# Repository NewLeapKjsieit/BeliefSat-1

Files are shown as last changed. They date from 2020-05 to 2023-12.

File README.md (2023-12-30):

# BeliefSat-1

BeliefSat-1 is a 2p-PocketQube standard student nano-satellite being developed by the undergraduate students of [**_K.J.Somaiya Institute of Engineering and Information Technology, Sion, Mumbai_** .](https://kjsieit.somaiya.edu/en) The satellite itself is a sub-part of team's proposal under [PS4-Orbital platform program](https://www.isro.gov.in/update/15-jun-2019/announcement-of-opportunity-ao-orbital-platform) of ISRO, wherein, team aims to demonstrate indegenously developed technologies for PocketQube standard nano-satellites. As a part of this demonstration, **BeliefSat** will be launched out of **SomaiyaPod** which is a Pocketqube standard deployer being indegenously developed at the institute. The unique construction technique, combination of COTS components for communication, on-board computer and power sub-systems , together constitute of **SomaiyaPQBus**, around which the satellite is being made, is also one of the technologies that the team wants to demonstrate and open-source to enable use by future missions.

## So what will BeliefSat do in space and what results it will give?

1. If it is successfully deployed out of the SomaiyaPod and completes startup procedure (it will be dead inside the Pod and will only get power after it is out of pod)and then sends a beacon; reliability of both deployer and the design of the satellite will be confirmed.
2. Every 1 minute, it will send a telemetry packet, which will have values from different COTS sensors. The team aims to project the activity of telemetry reception as a way of involving more students in to Software Defined Radio and RF in general.
3. It will have a functionality as of a amateur-radio digipeater. Which means if you hold a proper Amateur radio license then you can send a text message to the satellite and the satellite will repeat it (after delay of upto 10 seconds depending on other important processes running on-board). Making it a utility for Amateur radio community.
4. Not only it can digipeat a message it also has the functionality to repeat voice. For using this functionality you need a UHF transmitter and you can send a voice message to the satellite and the satellite will repeate it (after some delay depending on other important processes running on-board). It also will be a big utility for Amateur radio community.
5. If the satellite is able to operate for more than 3 months while responding to the commands and sending the health data at proper intervals, it will prove the reliablity of the unique design and set of COTS hardware used. Thus future mission could use flight proven hardwares for communication and power generation.

## What is it made of ?, What does it look like ?, What are its dimenssions and mass?

BeliefSat's structure is made by joining plates/PCBs(made out of FR4 material). This is a very novel approach in designing the structure of a satellite. Generally, satellites are made from Aluminium or its alloys, but using our novel approach we were able to design a very sturdy but cost effective sateliite. Although this technique is generally limited to nano-satellites. The PCBs that make the structure of our satellite have the solar panels and other components embedded in itself, so the complexity of assembly is minimized.

This is a concept render of our BeliefSat:

SATFOlded

The dimension of the BeliefSat is in accordance with the PocketQube Standards. This standard includes a base plate on which the satellite is mounted and then it slides out of
the satellite deployer via rails. As per the standards, our BeliefSat is 2P ie, Base plate is 58mm x 128mm x 1.6mm (WxLxH), whereas the satellite is 58mm x 128mm x 50mm (WxLxH).
The estimated mass of BeliefSat is around 450 grams. The dimensions of our deployer (SomaiyaPod) are 145mm x 200mm x 95mm (WxLxH).

## How is it powered?

The satellite is powered by AltaDevices Single Juntion cells ([which unfortunately are out of buisness as of date of writing](https://pv-magazine-usa.com/2019/12/31/shutdown-continues-at-hanergy-owned-alta-devices-high-efficiency-pv-pioneer/)). Each of these cell produce 0.25W power when illumniated at intensity of 1000W/m^2. There are 4 such cells on long sides and 2 on shorter sides. So when illuminated, satellite may produce 0.5W watt/1watt/>1W depending on the orientation. The power remaining after being used is then stored in 2 parallely connected [2600mah Samsung 18650 batteries](https://robokits.co.in/batteries-chargers/samsung-premium-li-ion-battery/3.7v-samsung-li-ion-batteries/samsung-icr-18650-26j-2600mah-li-ion-cell-original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). [SPV1040](https://www.st.com/en/power-management/spv1040.html) is used on every panel for maximum power point tracking and giving regulated voltage from the solar cells. The choice of SPV1040 was made based on flight history in [FossaSat-1](https://github.com/FOSSASystems/FOSSASAT-1). Now that AltaDevices cells won't be available in market, team will also be making one prototype with [SM141K06L by IXYS](https://www.digikey.com/product-detail/en/ixys/SM141K06L/SM141K06L-ND/9990462) and will be publishing test results for it too. 

## How does it communicate?

**_Transciever Specs_**
    **VHF**
-   **Name :** [DRA818V](http://www.dorji.com/products.php?Keyword=dra818v)
-   **Frequency Range :** 134~174 Mhz
-   **Channel Space :** 12.5/25 KHz
-   **TX Current :** 450/750 mA
-   **Temperature :** -20°C ~ +70°C
-   **Output Power :** +27/30 dbm
-   **Reciever Sensitivity :** -122 dbm (As per datasheet, observed sensititvity yet to be calculated)

    **UHF**
-   **Name :** [DRA818U](http://www.dorji.com/products.php?Keyword=dra818u)
-   **Frequency Range :** 400~470 Mhz
-   **Channel Space :** 25 KHz
-   **TX Current :** 450/750 mA
-   **Temperature :** -20°C ~ +70°C
-   **Output Power :** +27/30 dbm
-   **Reciever Sensitivity :** -122 dbm (As per datasheet, observed sensititvity yet to be calculated)
    _(UHF will only be used for voice repeater uplink)_
**_Antenna_**

Dipole made from measuring tape, which is in folded state during launch. Once in orbit, fishing cord which holds the antenna in folded position, is burnt by heating a resistor around which it is tied.

**_Link Budget_**

-   **Orbit Height :** 600 Km (proposed, may vary as per allocation by launch provider)
-   **Slant Range at 25 degree elevation :** 1213.4 Km (approximately)
-   **Free Space Path Loss at this distance for 145.825 MHz frequency :** 137.4 dbm
-   **Free Space Path Loss at this distance for 435.6 MHz frequency :** 146.9 dbm
-   **Received power neglecting mismatch,connector,atmospheric, pointing and polarization losses and receiving and transmitting antenna gains :** -118.2/-121.2 (op= 30/27dbm)
-   **Note :** A good directional antenna at receving groundstation (e.g. a 6 element yagi, plans for which will be released soon) can ensure the above mentioned losses are made up for and the signals can be received at even lower angles. However, to ensure best performance, circular polarized antennas copuled with a good LNA (e.g. [LNA4ALL](http://lna4all.blogspot.com/)) mounted over a Azimuth-Elevation antenna rotator (e.g. [Satnogs rotator](https://wiki.satnogs.org/SatNOGS_Rotator_v3)/[Sarcnet Rotator](https://www.sarcnet.org/rotator-mk2.html#RotatorMk2a)/[Yaesu G5500](https://www.yaesu.com/indexVS.cfm?cmd=DisplayProducts&ProdCatID=104&encProdID=79A89CEC477AA3B819EE02831F3FD5B8)/[WRAPS portable antenna rotator](https://ukamsat.files.wordpress.com/2013/12/wraps-mark-spencer-wa8sme-qst-jan-2014-copyright-arrl.pdf)) is recommended.

**_Data Rates in bps_**

-   **Telemetry Downlink :** 1200
-   **Digipeater Downlink :** 1200
-   **Command Uplink :** 1200
-   **Digipeater Uplink :** 1200

**_How the satellite complies with the requirment of turning off the transmitters when required ?_**
All the uplinks and downlinks occur on same frequency. Reciever is disabled while transmitting, to avoid interrupts to controller during the transmission, however, these transmissions last no more than 2 sec. This will ensure that one can relay a command during any pass. Also the transmitter is implemented to be active only when microcontroller is active, so if the main computer fails, the transmitter won't turn on. If the spacecraft computer is hung up for more than 8 sec, it resets along with the transciever. The automatic image capture mode is automatically turned off if battery voltage falls, thus adding extra layer of governance on the mode where long and continous transmission occurs. The satellite is designed to automatically turn off the microcontroller and thus the transciever in case of any thermal or short-circuit event. It is also protected against latchup situations caused by brown-outs or radiation flipping a bit, by the means of internal watchdog, which resets non-responsive or improperly finctioning controller after 8 sec. Whenever, required, satellites transmitters can be turned off until next command to turn those on by uplinking a command to do so. If the shut-down request comes when there is no pass over parent groundstation, the uplink packe format can be shared with a station which will have nearest pass.

## What are different packet types and packet formats ?

**_Telemetry Packet_**

**_APRS TELEMETRY FORMAT : The on-air packet telemetry format is as follows:_**

**T#sss,111,222,333,444,555,666,777,888,999,AAA,xxxxxxxx**
where,
-    sss : LSB of total number of system resets
-    111 : MSB of total number of system resets
-    222 : LSB of total number of resets induced by watch dog
-    333 : MSB of total number of resets induced by watch dog
-    444 : Temperature sensor 1 reading
-    555 : Temperature sensor 2 reading
-    666 : Gyro-sensor 1 reading
-    777 : Gyro-sensor 1 reading
-    888 : Gyro-sensor 1 reading
-    999 : Current reading
-    AAA : Voltage reading
-    xxxxxxxx : If the last two bits are 10 then digipeater is on and if they are 01 then voice repeater is on.

**References for converting Sensor data into readable format**

1. Temperature Sensor (DS18B20) :- [Datasheet](https://pdf1.alldatasheet.com/datasheet-pdf/view/58557/DALLAS/DS18B20.html)

2. Gyro Sensor (MPU-6050) :- [Datasheet](https://invensense.tdk.com/wp-content/uploads/2015/02/MPU-6000-Datasheet1.pdf)

3. Current/Power Sensor (INA219) :- [Datasheet](https://www.ti.com/lit/ds/symlink/ina219.pdf?ts=1593455980944&ref_url=https%253A%252F%252Fwww.google.com%252F)

**Reference for transreceivers**

1. DRA818V :- [Datasheet](http://www.dorji.com/docs/data/DRA818V.pdf)

2. DRA818U :- [Datasheet](http://www.dorji.com/docs/data/DRA818U.pdf)

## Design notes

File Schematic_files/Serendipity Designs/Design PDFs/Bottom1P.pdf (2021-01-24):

23-10-2020 11:05 PM C:\Users\Manas R. Sable\Desktop\PROTOTYPE\Final PCBs\BOTTOM_1P.sch (Sheet: 1/1) | 10K

A

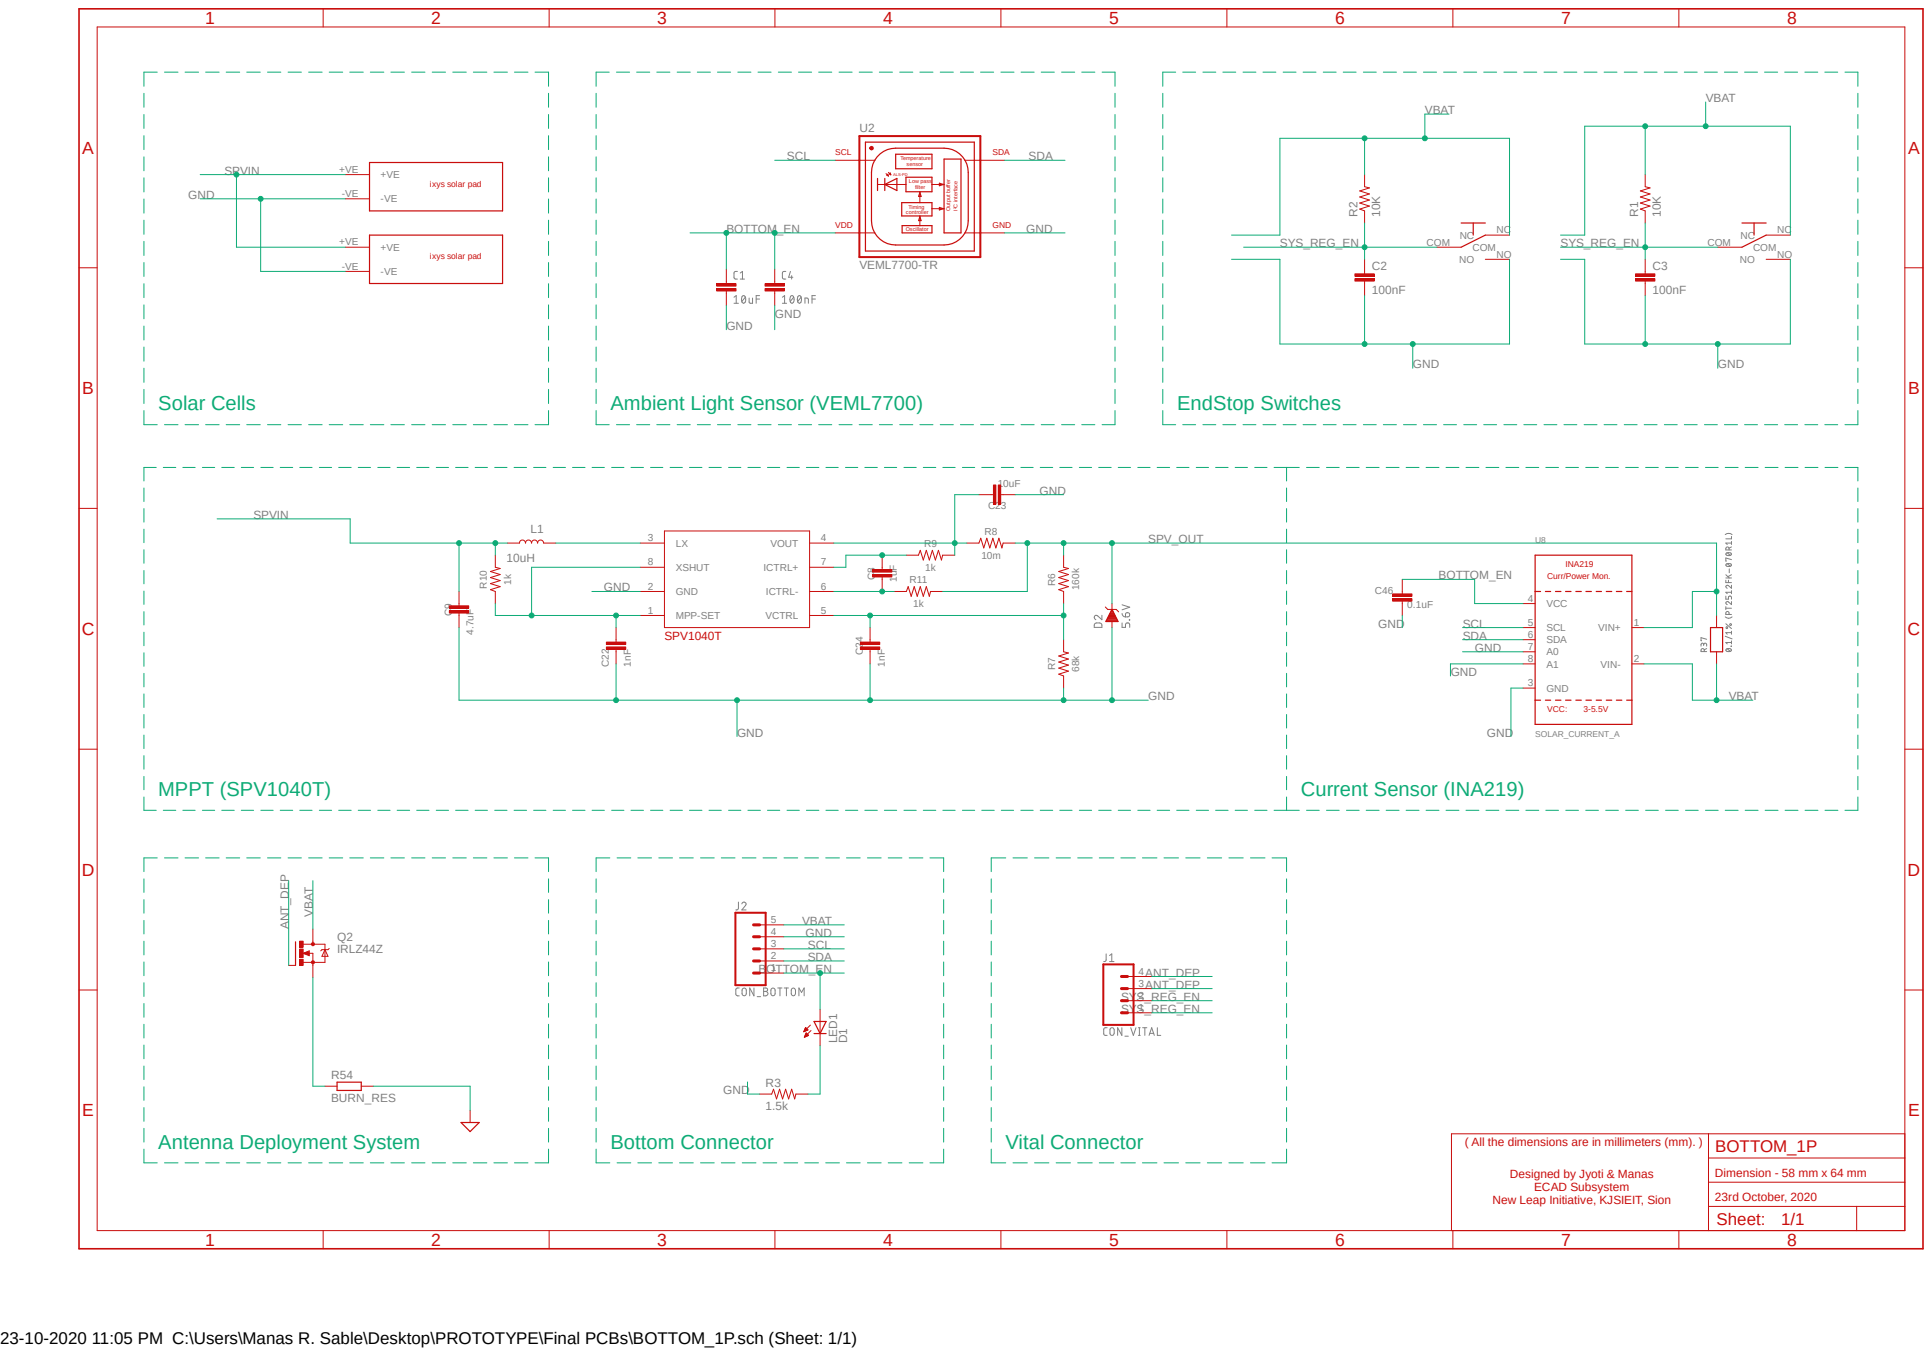
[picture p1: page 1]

( All the dimensions are in millimeters (mm). )

Designed by Jyoti & Manas
ECAD Subsystem

New Leap Initiative, KJSIEIT, Sion

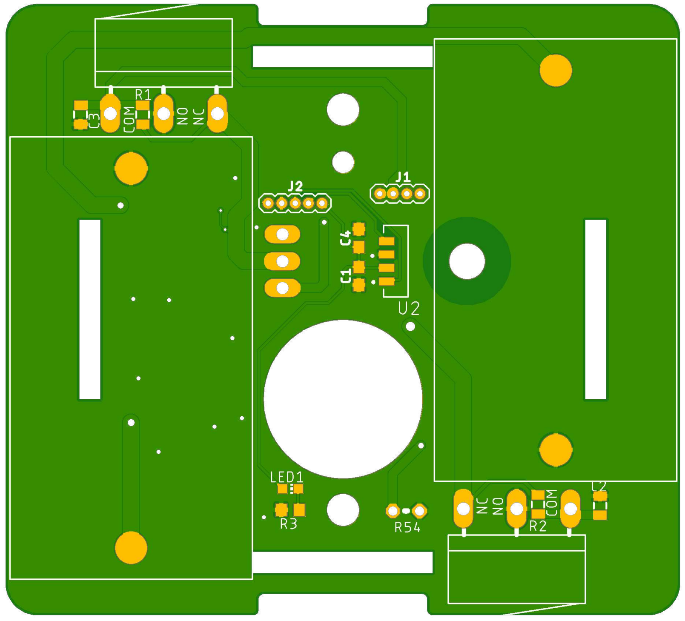
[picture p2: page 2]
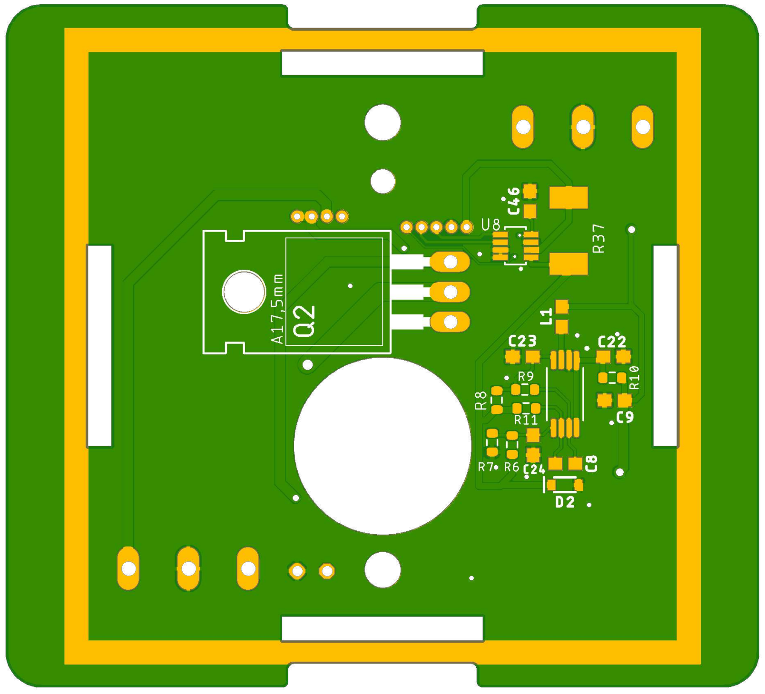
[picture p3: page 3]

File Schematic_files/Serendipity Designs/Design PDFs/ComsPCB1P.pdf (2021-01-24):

A

A

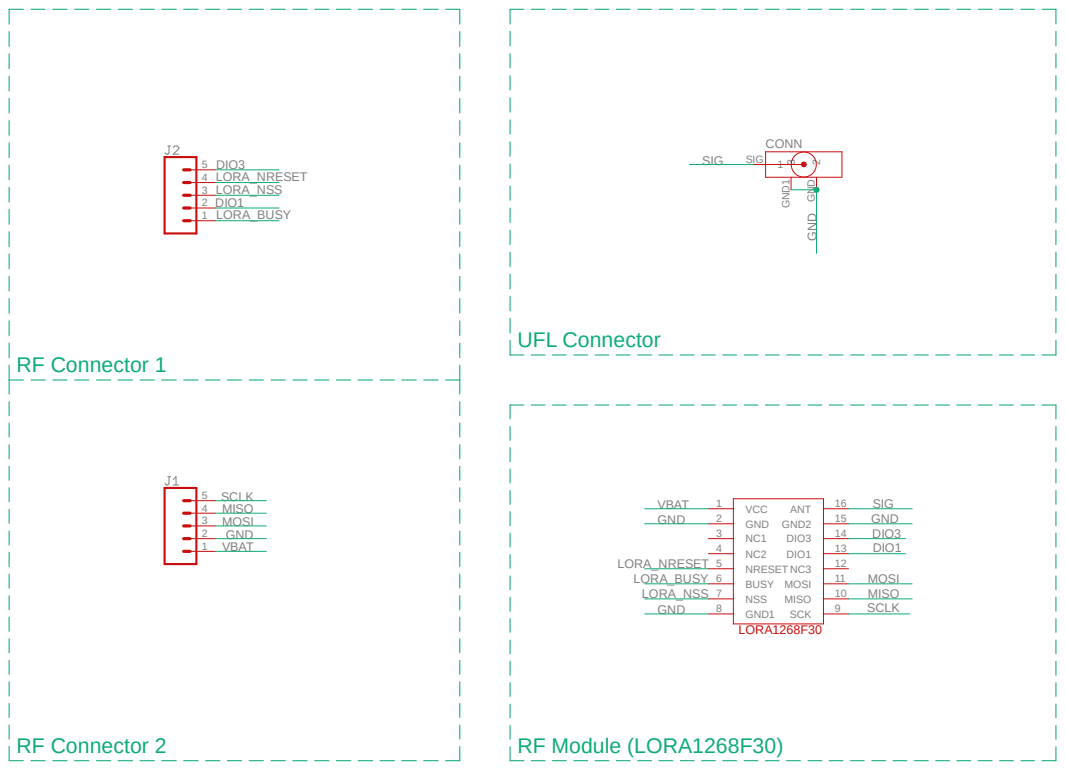
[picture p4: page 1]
1 SIG; 3 GND¹; 2 GND; CONN; VCC 1; GND 2; NRESET 5; BUSY 6; NSS 7; GND1 8; SCK; 9 MISO; 10 MOSI; 12 DIO1; 13 DIO3; 14 GND2; 15 ANT; 16 VBAT; VBAT; GND; MOSI; MISO; SCLK; LORA_BUSY; LORA_NSS; LORA_NRESET; SIG; DIO3; DIO1; LORA1268F30; ComsPCB (1); RF Module (LORA1268F30); UFL Connector; RF Connector 1; RF Connector 2

( All the dimensions are in millimeters (mm). )

Designed by Jyoti & Manas
ECAD Subsystem

Dimension - 42 mm x 44 mm
24th October, 2020
Sheet:

New Leap Initiative, KJSIEIT, Sion

24-10-2020 07:42 PM C:\Users\Manas R. Sable\Desktop\PROTOTYPE\Final PCBs\ComsPCB (1).sch (Sheet: 1/1)

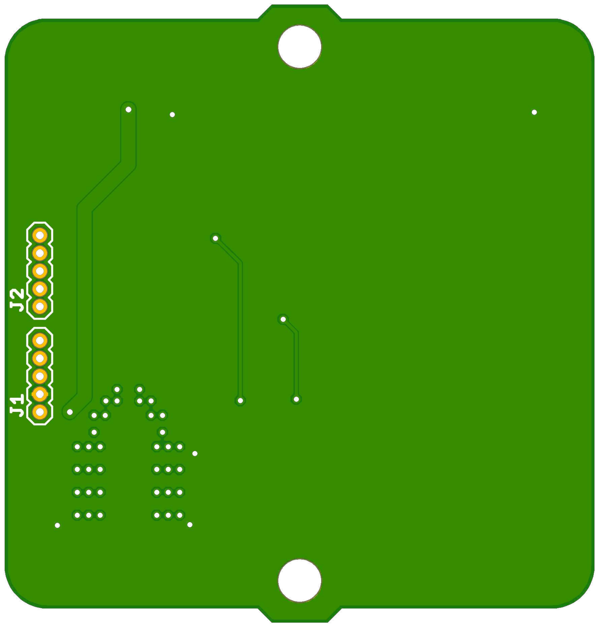
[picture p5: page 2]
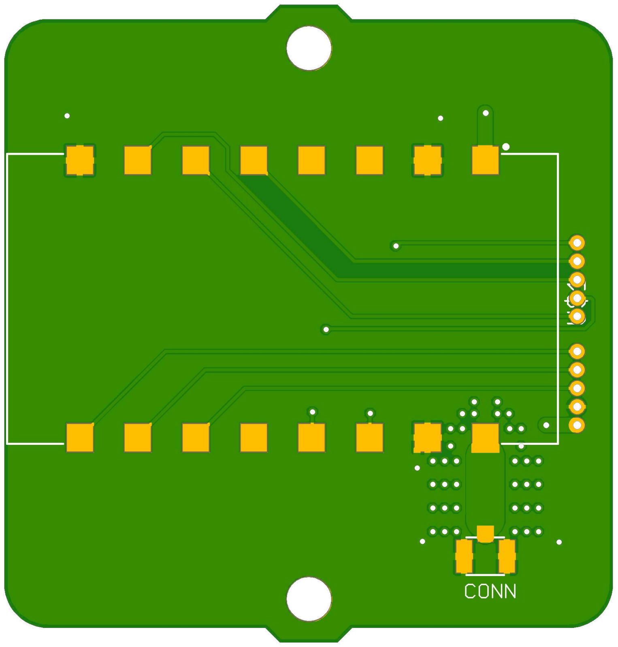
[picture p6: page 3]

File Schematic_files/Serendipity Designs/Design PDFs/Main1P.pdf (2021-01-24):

A

A

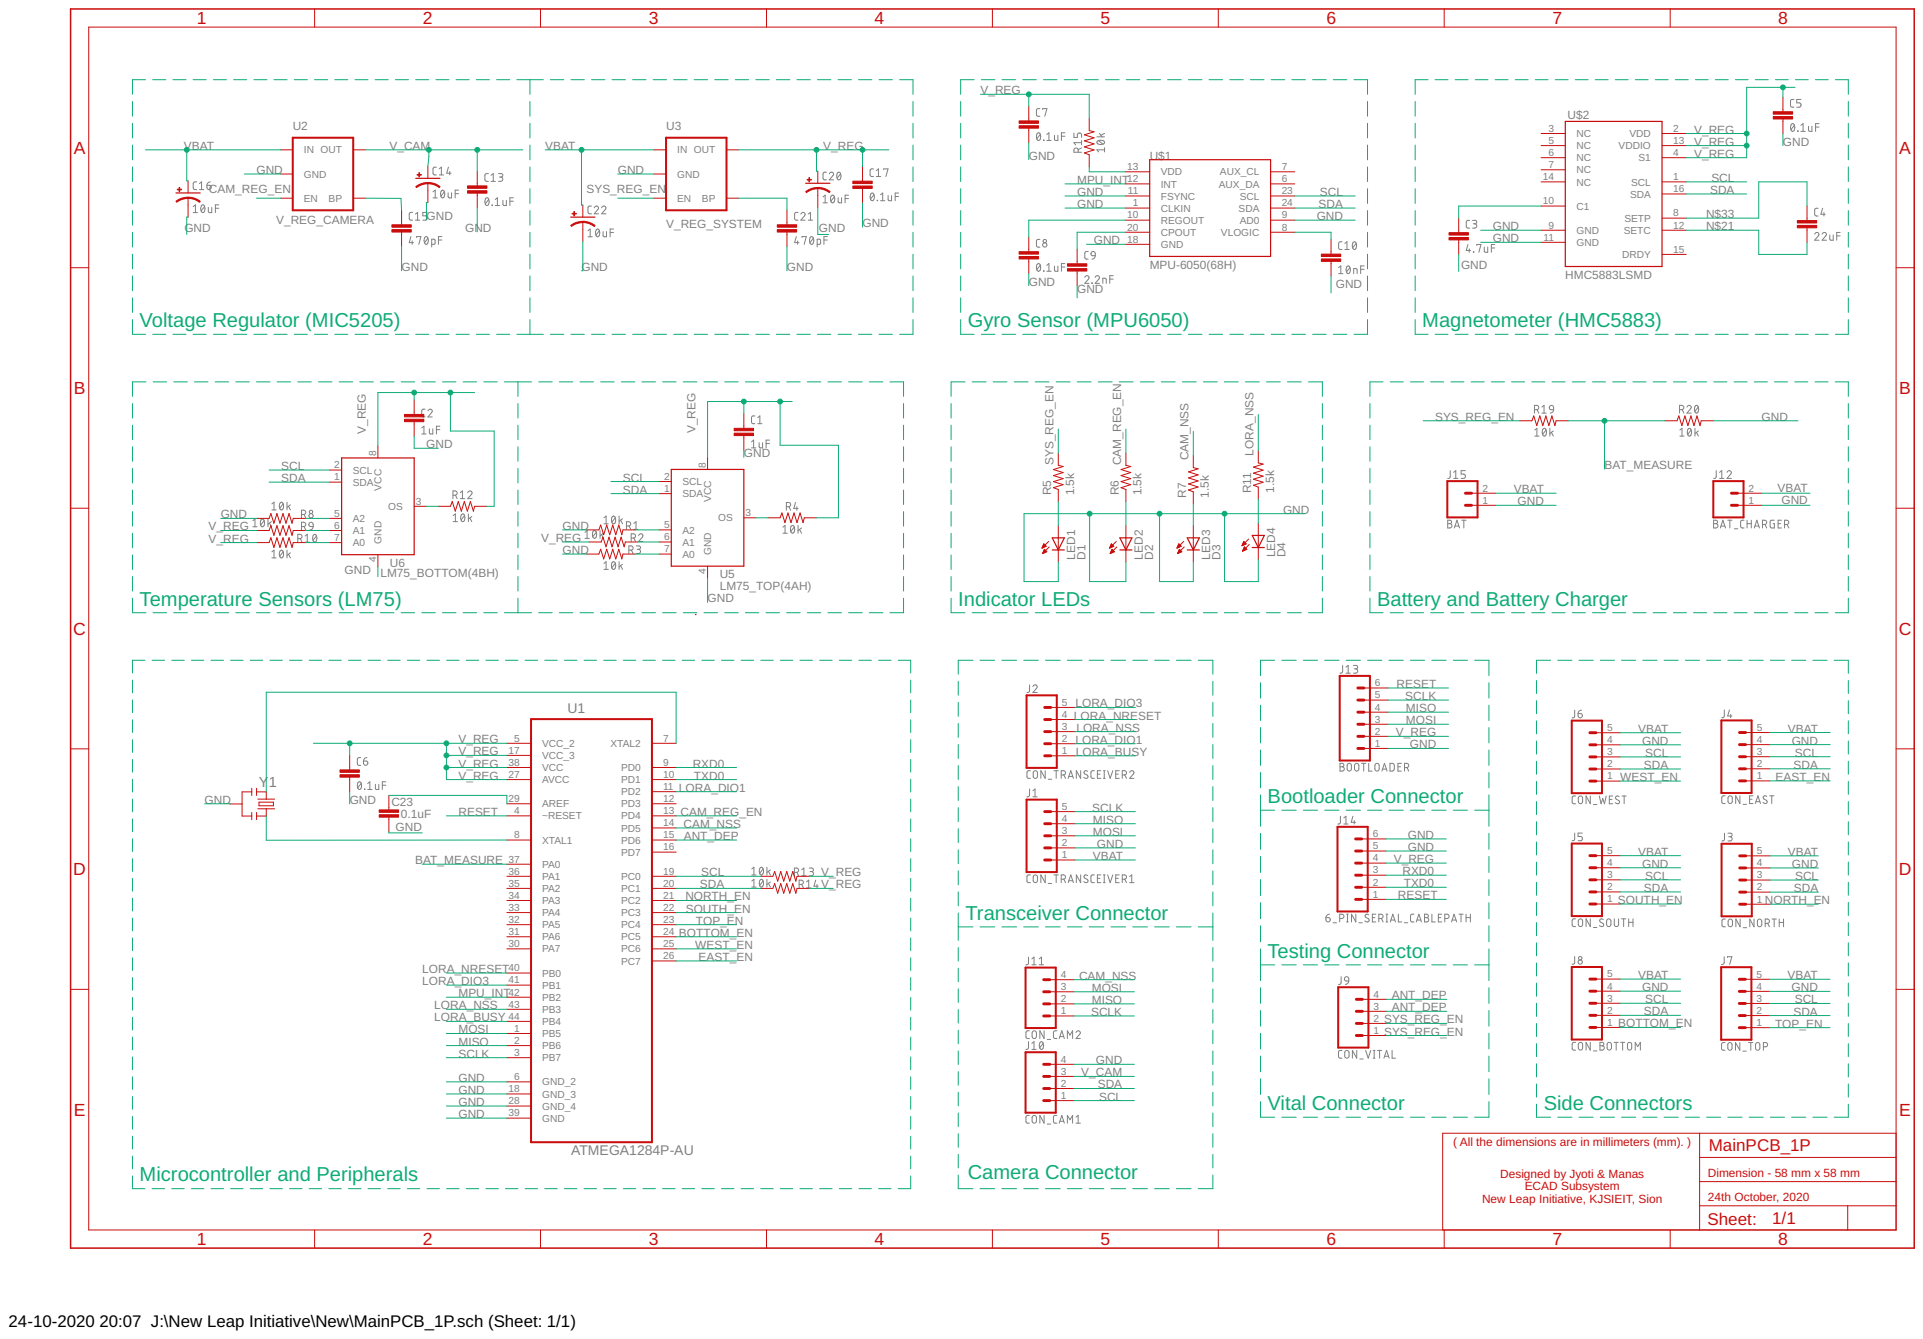
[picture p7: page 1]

( All the dimensions are in millimeters (mm). )

Designed by Jyoti & Manas ECAD Subsystem

24-10-2020 20:07 J:\New Leap Initiative\New\MainPCB_1P.sch (Sheet: 1/1)

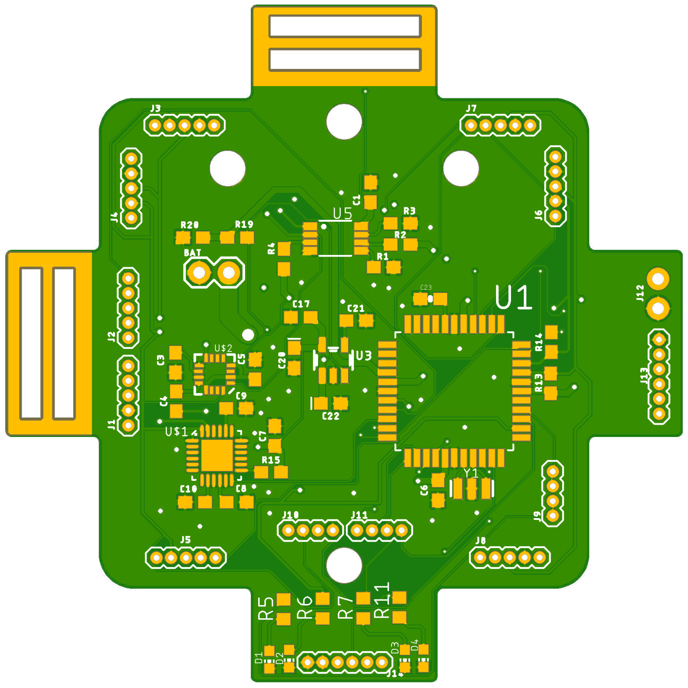
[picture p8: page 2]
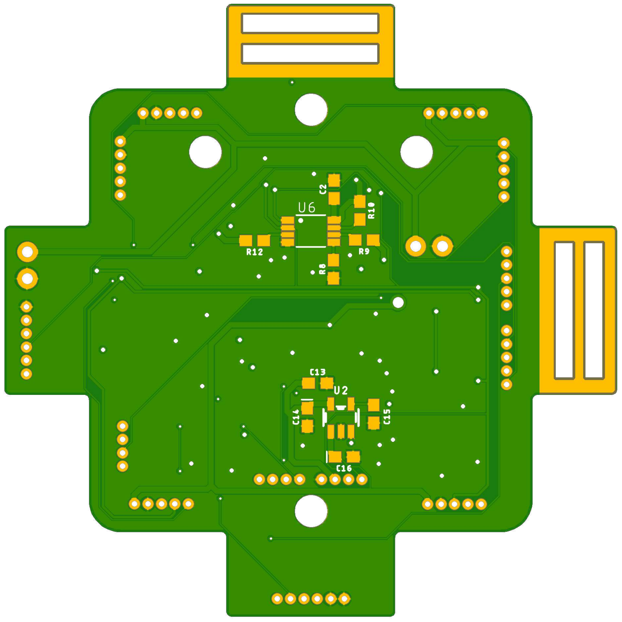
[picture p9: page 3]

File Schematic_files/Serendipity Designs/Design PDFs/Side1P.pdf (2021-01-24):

A

A

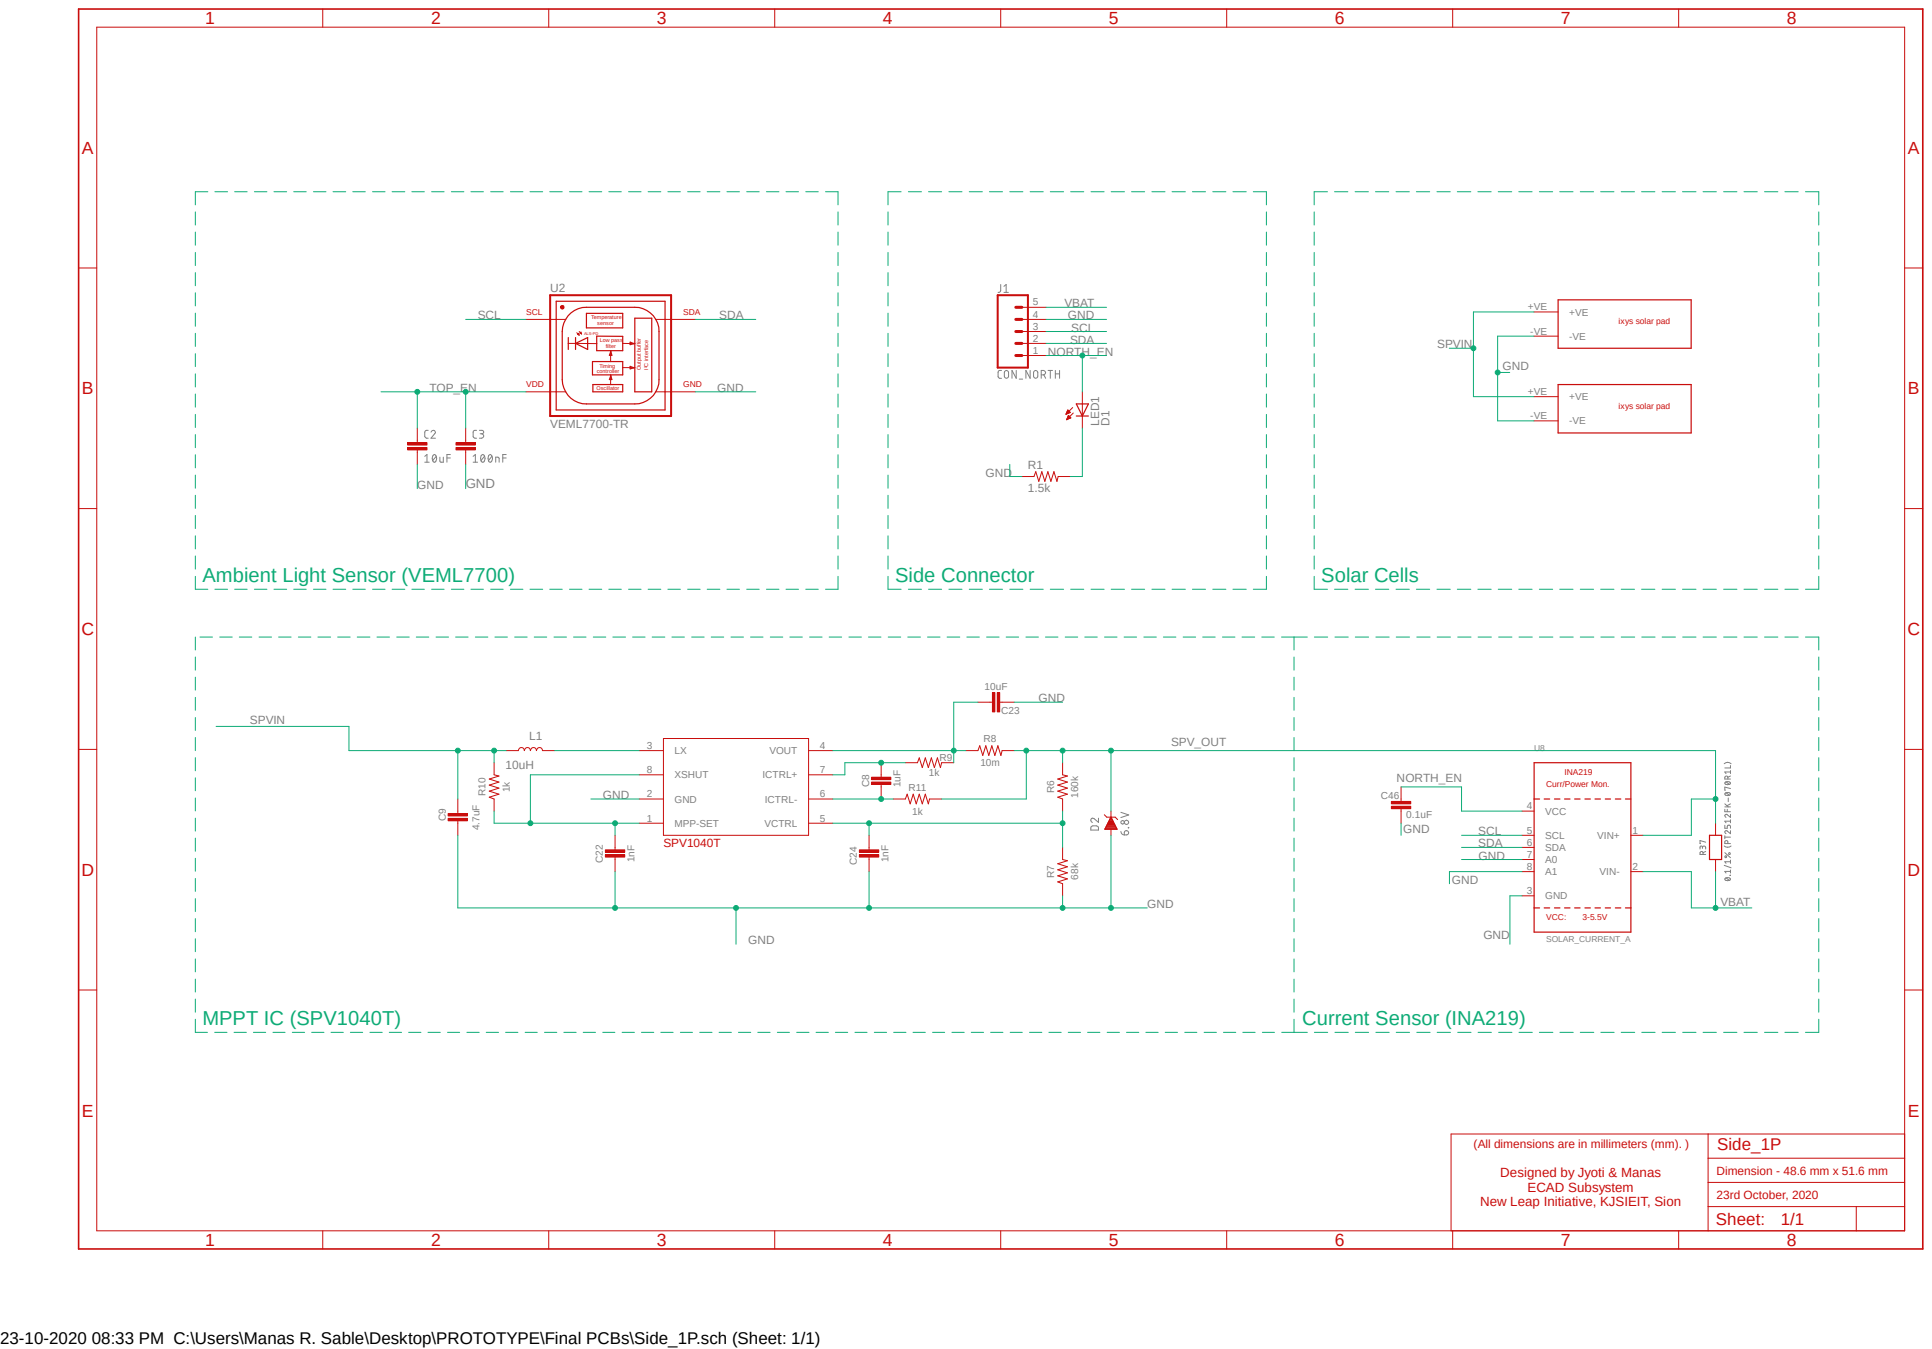
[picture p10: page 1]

(All dimensions are in millimeters (mm). )
Designed by Jyoti & Manas
ECAD Subsystem

New Leap Initiative, KJSIEIT, Sion

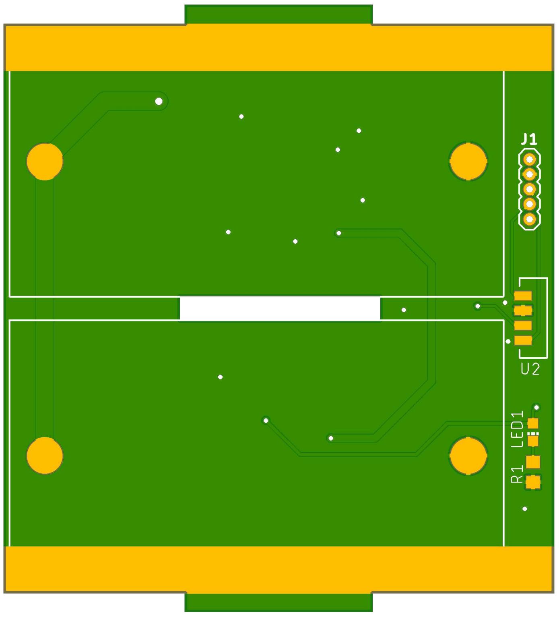
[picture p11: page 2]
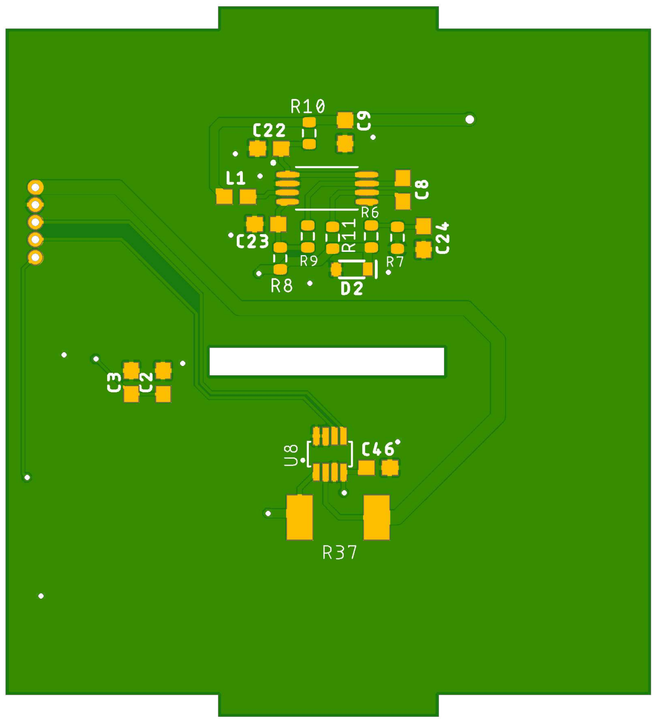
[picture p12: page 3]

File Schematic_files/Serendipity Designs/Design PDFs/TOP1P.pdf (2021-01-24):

A

A

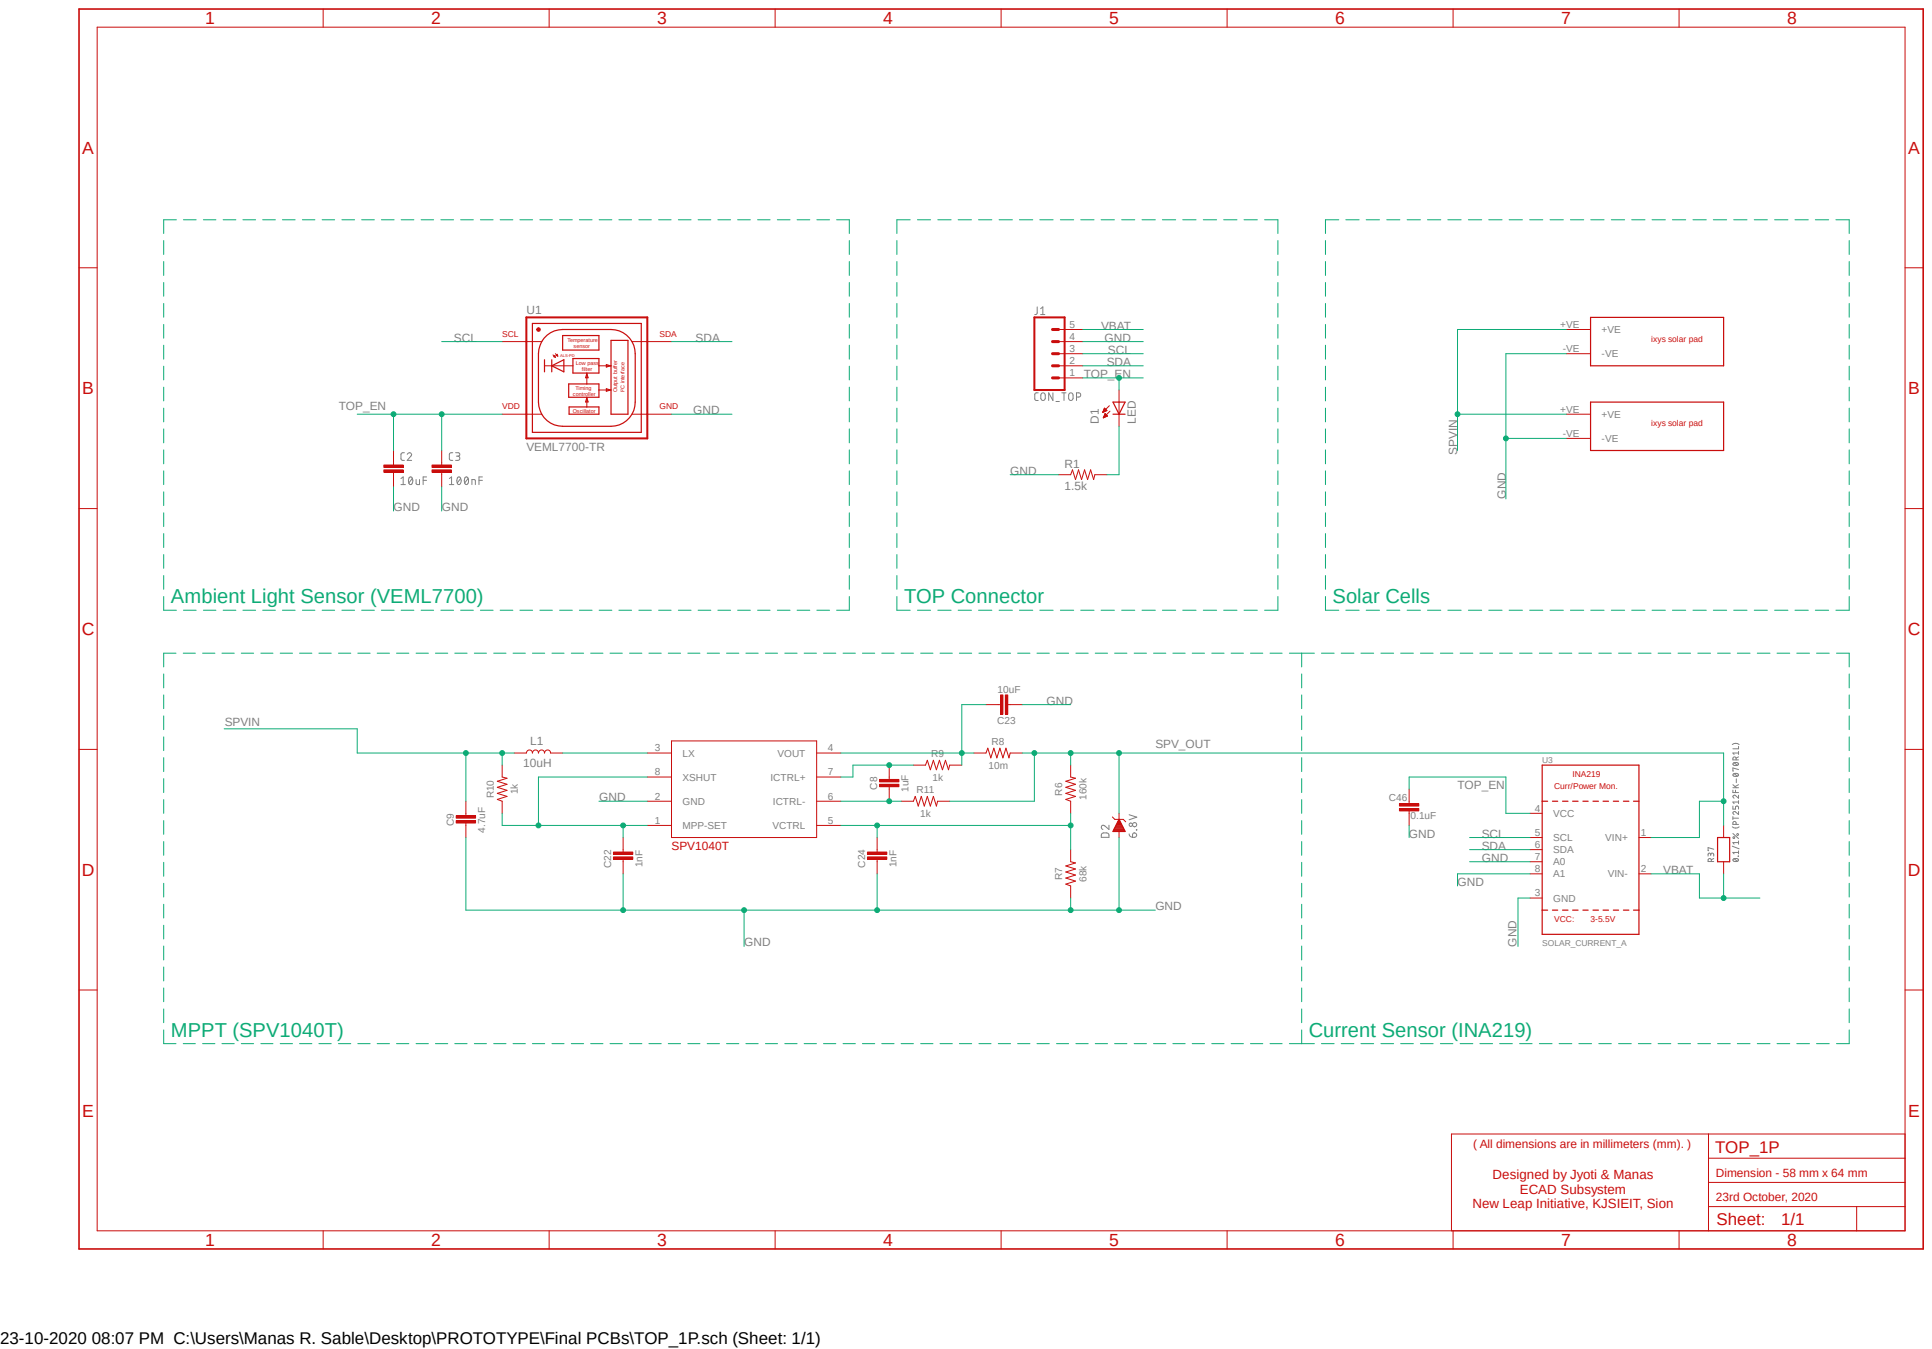
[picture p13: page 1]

( All dimensions are in millimeters (mm). )

Designed by Jyoti & Manas
ECAD Subsystem

New Leap Initiative, KJSIEIT, Sion

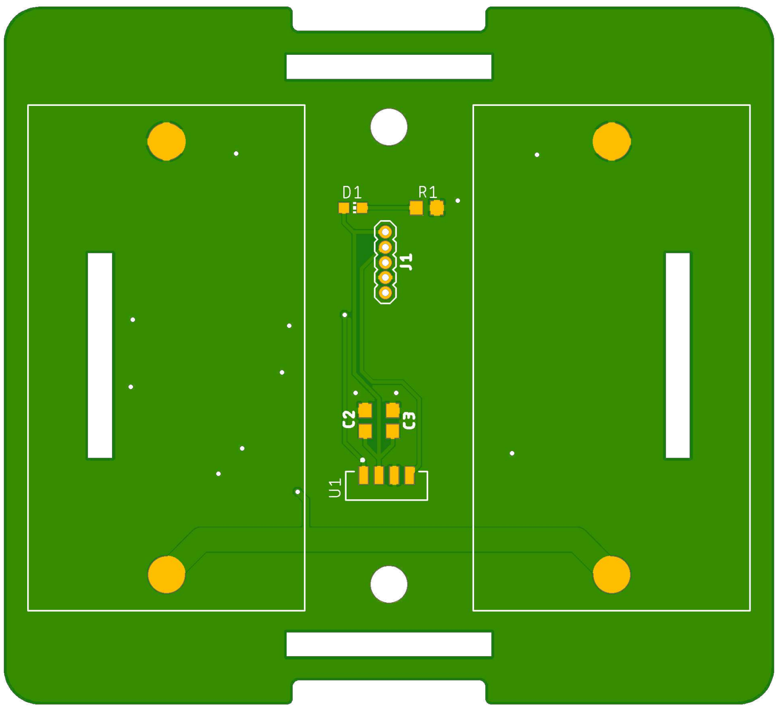
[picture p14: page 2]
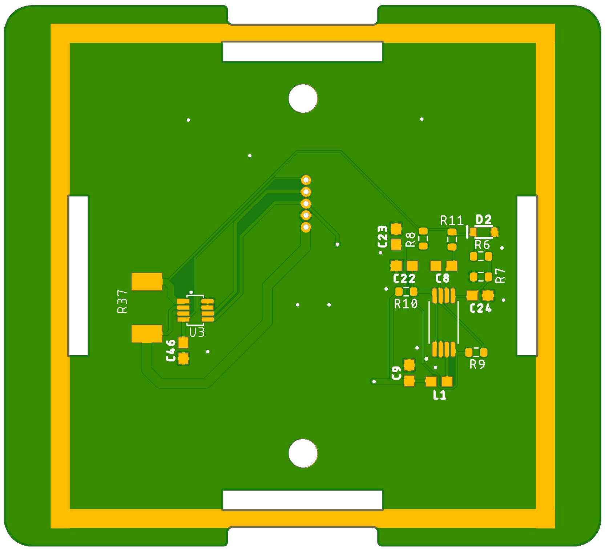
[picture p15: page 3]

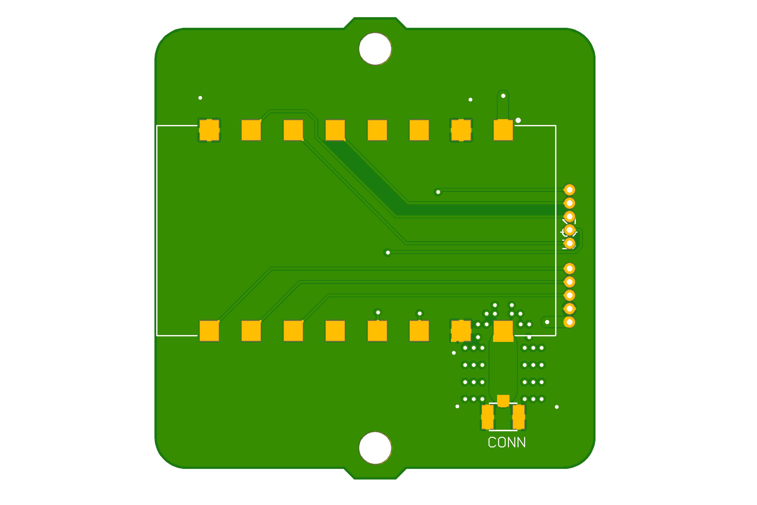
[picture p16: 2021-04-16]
Schematic_files/Serendipity Designs/ComsPCB_1P_bottom.png

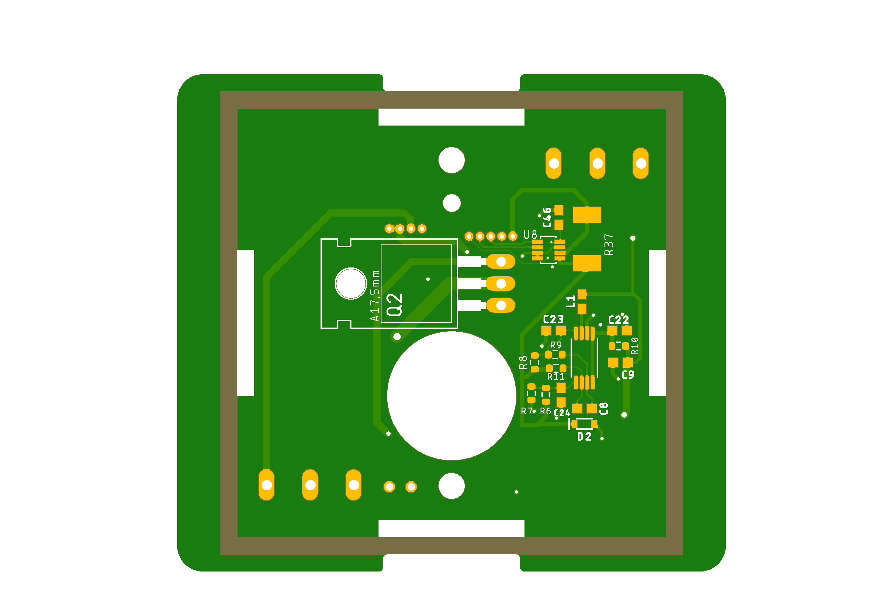
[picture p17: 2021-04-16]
Schematic_files/Serendipity Designs/BOTTOM_1P_BOTTOM.png

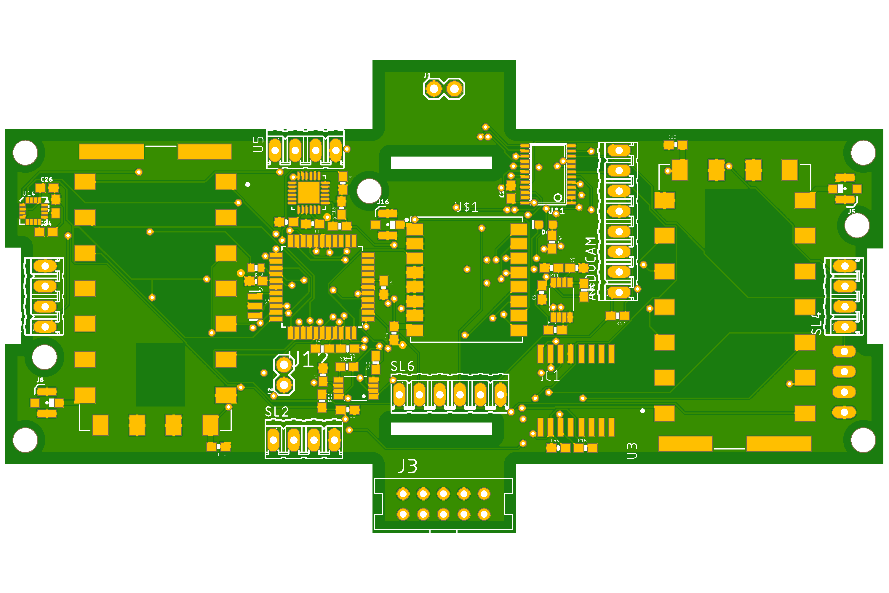
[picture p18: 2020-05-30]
Schematic_files/PS4_Proposal_Schem/MainCPCB003.png

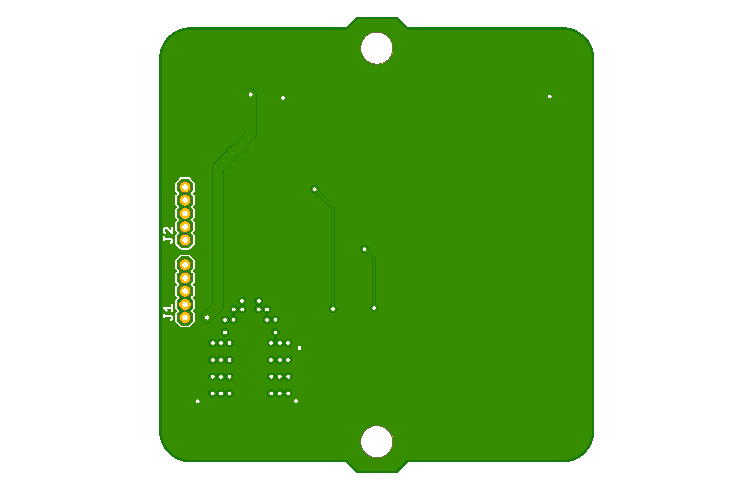
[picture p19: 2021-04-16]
Schematic_files/Serendipity Designs/ComsPCB_1P_top.png

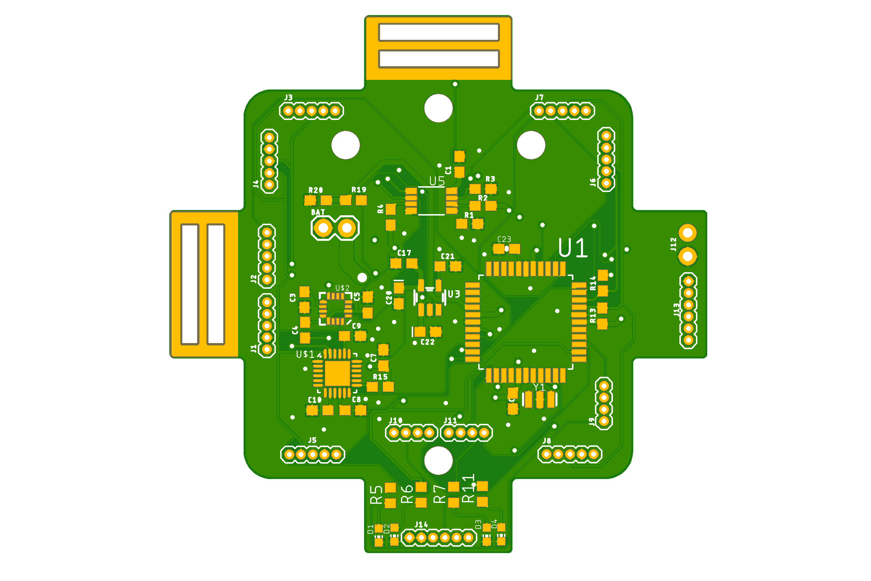
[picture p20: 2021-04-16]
Schematic_files/Serendipity Designs/MainPCB_1P_top.png

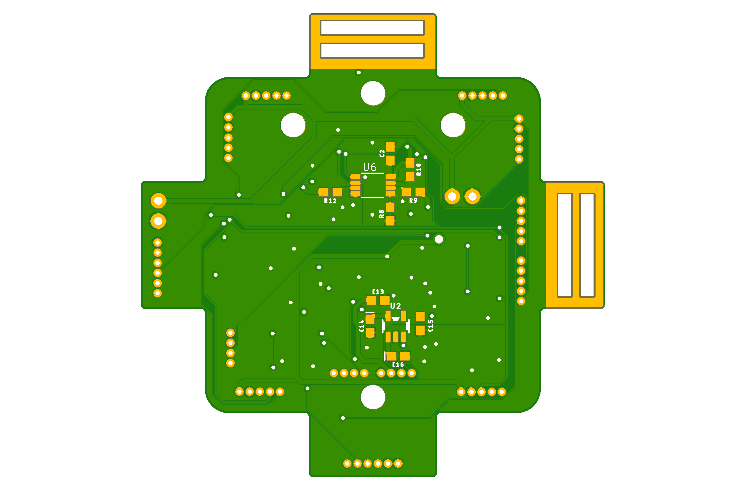
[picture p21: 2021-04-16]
Schematic_files/Serendipity Designs/MainPCB_1P_bottom.png

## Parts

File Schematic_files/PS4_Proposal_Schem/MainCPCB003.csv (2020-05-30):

Part | Value | Device | Package | Description | AVAILABILITY | DESCRIPTION | MF | MP | MPN | OC_FARNELL | OC_NEWARK | PACKAGE | PRICE | PROD_ID | SF_ID | VALUE
ARDUCAM |  | M08 | 08P | AMP QUICK CONNECTOR |  |  |  |  |  | unknown | unknown
C1 | 0.1uF | CAP0603-CAP | 0603-CAP | Capacitor
C2 | 10uF | 10UF-POLAR-0603-6.3V-20%(TANT) | 0603-POLAR | 10.0µF polarized capacitors |  |  |  |  |  |  |  |  |  | CAP-13210 |  | 10uF
C3 | 10uF | 10UF-POLAR-0603-6.3V-20%(TANT) | 0603-POLAR | 10.0µF polarized capacitors |  |  |  |  |  |  |  |  |  | CAP-13210 |  | 10uF
C4 | 0.1uF | CAP0603-CAP | 0603-CAP | Capacitor
C5 | 0.1uF | CAP0603-CAP | 0603-CAP | Capacitor
C6 | 1uF | CAP0603-CAP | 0603-CAP | Capacitor
C7 | 10uF | 10UF-POLAR-0603-6.3V-20%(TANT) | 0603-POLAR | 10.0µF polarized capacitors |  |  |  |  |  |  |  |  |  | CAP-13210 |  | 10uF
C8 | 10uF | 10UF-POLAR-0603-6.3V-20%(TANT) | 0603-POLAR | 10.0µF polarized capacitors |  |  |  |  |  |  |  |  |  | CAP-13210 |  | 10uF
C9 | 2.2nF | CAP0603-CAP | 0603-CAP | Capacitor
C10 | 0.1uF | CAP0603-CAP | 0603-CAP | Capacitor
C11 | 10nF | CAP0603-CAP | 0603-CAP | Capacitor
C12 | 0.1uF | CAP0603-CAP | 0603-CAP | Capacitor
C13 | 0.1uF | CAP0603-CAP | 0603-CAP | Capacitor
C14 | 0.1uF | CAP0603-CAP | 0603-CAP | Capacitor
C15 | 0.1uF | CAP0603-CAP | 0603-CAP | Capacitor
C16 | 22uF | 10UF-0603-6.3V-20% | 0603 | 10.0µF ceramic capacitors |  |  |  |  |  |  |  |  |  | CAP-11015 |  | 10uF
C17 | 10uF | 10UF-0603-6.3V-20% | 0603 | 10.0µF ceramic capacitors |  |  |  |  |  |  |  |  |  | CAP-11015 |  | 10uF
C18 | 0.1uF | 10UF-0603-6.3V-20% | 0603 | 10.0µF ceramic capacitors |  |  |  |  |  |  |  |  |  | CAP-11015 |  | 10uF
C19 | 470pF | CAP0603-CAP | 0603-CAP | Capacitor
C20 | 22uF | 10UF-0603-6.3V-20% | 0603 | 10.0µF ceramic capacitors |  |  |  |  |  |  |  |  |  | CAP-11015 |  | 10uF
C21 | 0.1uF | CAP0603-CAP | 0603-CAP | Capacitor
C22 | 470pF | CAP0603-CAP | 0603-CAP | Capacitor
C23 | 4.7uF | 0.18UF-0603-10V-10% | 0603 | 0.18µF ceramic capacitor |  |  |  |  |  |  |  |  |  | CAP-12380 |  | 0.18uF
C24 | .22uF | 0.18UF-0603-10V-10% | 0603 | 0.18µF ceramic capacitor |  |  |  |  |  |  |  |  |  | CAP-12380 |  | 0.18uF
C25 | 10uF | 10UF-0603-6.3V-20% | 0603 | 10.0µF ceramic capacitors |  |  |  |  |  |  |  |  |  | CAP-11015 |  | 10uF
C26 | 0.1uF | 0.18UF-0603-10V-10% | 0603 | 0.18µF ceramic capacitor |  |  |  |  |  |  |  |  |  | CAP-12380 |  | 0.18uF
C45 | 0.1uF | 10UF-0603-6.3V-20% | 0603 | 10.0µF ceramic capacitors |  |  |  |  |  |  |  |  |  | CAP-11015 |  | 10uF
C52 | 10uF | 10UF-0603-6.3V-20% | 0603 | 10.0µF ceramic capacitors |  |  |  |  |  |  |  |  |  | CAP-11015 |  | 10uF
C55 | 1uF | CAP0603-CAP | 0603-CAP | Capacitor
C56 | 1uF | CAP0603-CAP | 0603-CAP | Capacitor
D1 | GREEN | LED-GREEN0603 | LED-0603 | Green SMD LED |  |  |  |  |  |  |  |  |  | DIO-00821 |  | GREEN
D2 | GREEN | LED-GREEN0603 | LED-0603 | Green SMD LED |  |  |  |  |  |  |  |  |  | DIO-00821 |  | GREEN
D3 | GREEN | LED-GREEN0603 | LED-0603 | Green SMD LED |  |  |  |  |  |  |  |  |  | DIO-00821 |  | GREEN
D4 | GREEN | LED-GREEN0603 | LED-0603 | Green SMD LED |  |  |  |  |  |  |  |  |  | DIO-00821 |  | GREEN
D5 | GREEN | LED-GREEN0603 | LED-0603 | Green SMD LED |  |  |  |  |  |  |  |  |  | DIO-00821 |  | GREEN
D6 | GREEN | LED-GREEN0603 | LED-0603 | Green SMD LED |  |  |  |  |  |  |  |  |  | DIO-00821 |  | GREEN
D8 | GREEN | LED-GREEN0603 | LED-0603 | Green SMD LED |  |  |  |  |  |  |  |  |  | DIO-00821 |  | GREEN
D9 | GREEN | LED-GREEN0603 | LED-0603 | Green SMD LED |  |  |  |  |  |  |  |  |  | DIO-00821 |  | GREEN
IC1 | DS3231/SO | DS3231/SO | SO16W | The DS3231 is a low-cost, extremely accurate I²C real-time clock (RTC) with an integrated temperature-compensated crystal oscillator (TCXO) and crystal. The device incorporates a battery input, and maintains accurate timekeeping when main power to the device is interrupted. | Unavailable |  | Maxim Integrated | DS3231 |  |  |  | SOIC-16 Maxim Integrated | None
J1 | Charger | CONN_02 | 1X02 | Multi connection point. Often used as Generic Header-pin footprint for 0.1 inch spaced/style header connections
J2 | Battery2 | CONN_02 | 1X02 | Multi connection point. Often used as Generic Header-pin footprint for 0.1 inch spaced/style header connections
J3 |  | SOCKET-10V | S10V | 10 pin PCB Socket (3m 85xx/51xx)
J5 | U.FL_TX | U.FL2PIN | U.FL | SMD Antenna Connector - U.FL |  |  |  |  |  |  |  |  |  | CONN-09193 | WRL-09144 | U.FL
J6 | U.FL_RX | U.FL2PIN | U.FL | SMD Antenna Connector - U.FL |  |  |  |  |  |  |  |  |  | CONN-09193 | WRL-09144 | U.FL
J16 | U.FL_LORA | U.FL2PIN | U.FL | SMD Antenna Connector - U.FL |  |  |  |  |  |  |  |  |  | CONN-09193 | WRL-09144 | U.FL
L1 | 2.2uH | INDUCTOR-0603-33NH | 0603 | Inductors |  |  |  |  |  |  |  |  |  | NDUC-07874 |  | 33nH/±5%/500mA
L3 | 2.2uH | INDUCTOR-0603-33NH | 0603 | Inductors |  |  |  |  |  |  |  |  |  | NDUC-07874 |  | 33nH/±5%/500mA
R1 | 1.5k | RESISTOR0603-RES | 0603-RES | Resistor
R2 | 1.5k | RESISTOR0603-RES | 0603-RES | Resistor
R3 | 10k | RESISTOR0603-RES | 0603-RES | Resistor
R4 | 10k | RESISTOR0603-RES | 0603-RES | Resistor
R6 | 1.5k | RESISTOR0603-RES | 0603-RES | Resistor
R7 | 10k | RESISTOR0603-RES | 0603-RES | Resistor
R8 | 10k | RESISTOR0402-RES | 0402-RES | Resistor
R9 | 0.1/1% (PT2512FK-070R1L) | RESISTOR2512 | 2512 | Resistors
R10 | 10k | RESISTOR0402-RES | 0402-RES | Resistor
R11 | 10k | RESISTOR0603-RES | 0603-RES | Resistor
R12 | 10k | RESISTOR0603-RES | 0603-RES | Resistor
R13 | 1.5k | RESISTOR0603-RES | 0603-RES | Resistor
R14 | 10k | RESISTOR0603-RES | 0603-RES | Resistor
R15 | 10k | RESISTOR0603-RES | 0603-RES | Resistor
R16 | 10k | RESISTOR0603-RES | 0603-RES | Resistor
R17 | 1.5k | RESISTOR0603-RES | 0603-RES | Resistor
R18 | 10k | RESISTOR0603-RES | 0603-RES | Resistor
R19 | 1.5k | RESISTOR0603-RES | 0603-RES | Resistor
R20 | 1.5k | RESISTOR0603-RES | 0603-RES | Resistor
R36 | 0.1/1% (PT2512FK-070R1L) | RESISTOR2512 | 2512 | Resistors
R42 | 10k | RESISTOR0603-RES | 0603-RES | Resistor
R44 | 10k | RESISTOR0603-RES | 0603-RES | Resistor
R50 | 10k | RESISTOR0603-RES | 0603-RES | Resistor
R51 | 10k | RESISTOR0603-RES | 0603-RES | Resistor
R52 | 10k | RESISTOR0603-RES | 0603-RES | Resistor
R53 | 10k | RESISTOR0603-RES | 0603-RES | Resistor
SL1 |  | M04 | 04P | AMP QUICK CONNECTOR |  |  |  |  |  | unknown | unknown
SL2 |  | M04 | 04P | AMP QUICK CONNECTOR |  |  |  |  |  | unknown | unknown
SL3 |  | M04 | 04P | AMP QUICK CONNECTOR |  |  |  |  |  | unknown | unknown
SL4 |  | M04 | 04P | AMP QUICK CONNECTOR |  |  |  |  |  | unknown | unknown
SL5 |  | M04 | 04P | AMP QUICK CONNECTOR |  |  |  |  |  | unknown | unknown
SL6 |  | M06 | 06P | AMP QUICK CONNECTOR |  |  |  |  |  | unknown | unknown
U$1 | DRF1268 | DRF1268 | RESCAV180P1570X1400X300-16
U1 | GYRO-SENSOR | MPU-6050-1 | QFN-24-4MM2
U2 | TEMP_BAT(4C) | LM75BDP | SOT505-1 | Digital temperature sensor and thermal watchdog | Unavailable |  | NXP Semiconductors | LM75B |  |  |  | None | None
U3 | DRA818U_TX | DRA818U | DORJI_DRA818U | VHF Band Voice Transceiver Module | Unavailable |  | DORJI | DRA818V |  |  |  | Package Analog Devices | None
U4 | REG_UC | V_REG_LDOSMD | SOT23-5 | Voltage Regulator LDO
U5 | DRA818U_RX | DRA818U | DORJI_DRA818U | VHF Band Voice Transceiver Module | Unavailable |  | DORJI | DRA818V |  |  |  | Package Analog Devices | None
U6 | REG_BUS | VREG_LM3671 | SOT23-5 | LM3671 - 600mA DC-DC Step-Down Converter
U7 | Current_system(40) | INA219 | SOT23-8 | INA219 - I2C Current/Power Monitor
U8 | REG_PAYLOAD | VREG_LM3671 | SOT23-5 | LM3671 - 600mA DC-DC Step-Down Converter
U9 | Current_payload(46) | INA219 | SOT23-8 | INA219 - I2C Current/Power Monitor
U10 | REG_CAM | V_REG_LDOSMD | SOT23-5 | Voltage Regulator LDO
U11 | TCA9548APWR | TCA9548A | TSSOP24 | TCA9548A I2C Multiplexer
U12 | ATMEGA1284P-AU | ATMEGA1284P-AU | QFP80P1200X1200X120-44N | Microcontroller with Programmable Flash | Unavailable | AVR AVR® ATmega Microcontroller IC 8-Bit 20MHz 128KB _64K x 16_ FLASH 44-TQFP _10x10_ | Microchip | ATMEGA1284P-AU |  |  |  | TQFP-44 Microchip | None
U13 | TEMP_UC(4D) | LM75BDP | SOT505-1 | Digital temperature sensor and thermal watchdog | Unavailable |  | NXP Semiconductors | LM75B |  |  |  | None | None
U14 | HMC5883LSMD | HMC5883LSMD | 16LPCC | 3 Axis Digital Compass IC
Y2 | RESONATORSMD | RESONATORSMD | RESONATOR-SMD | Resonator

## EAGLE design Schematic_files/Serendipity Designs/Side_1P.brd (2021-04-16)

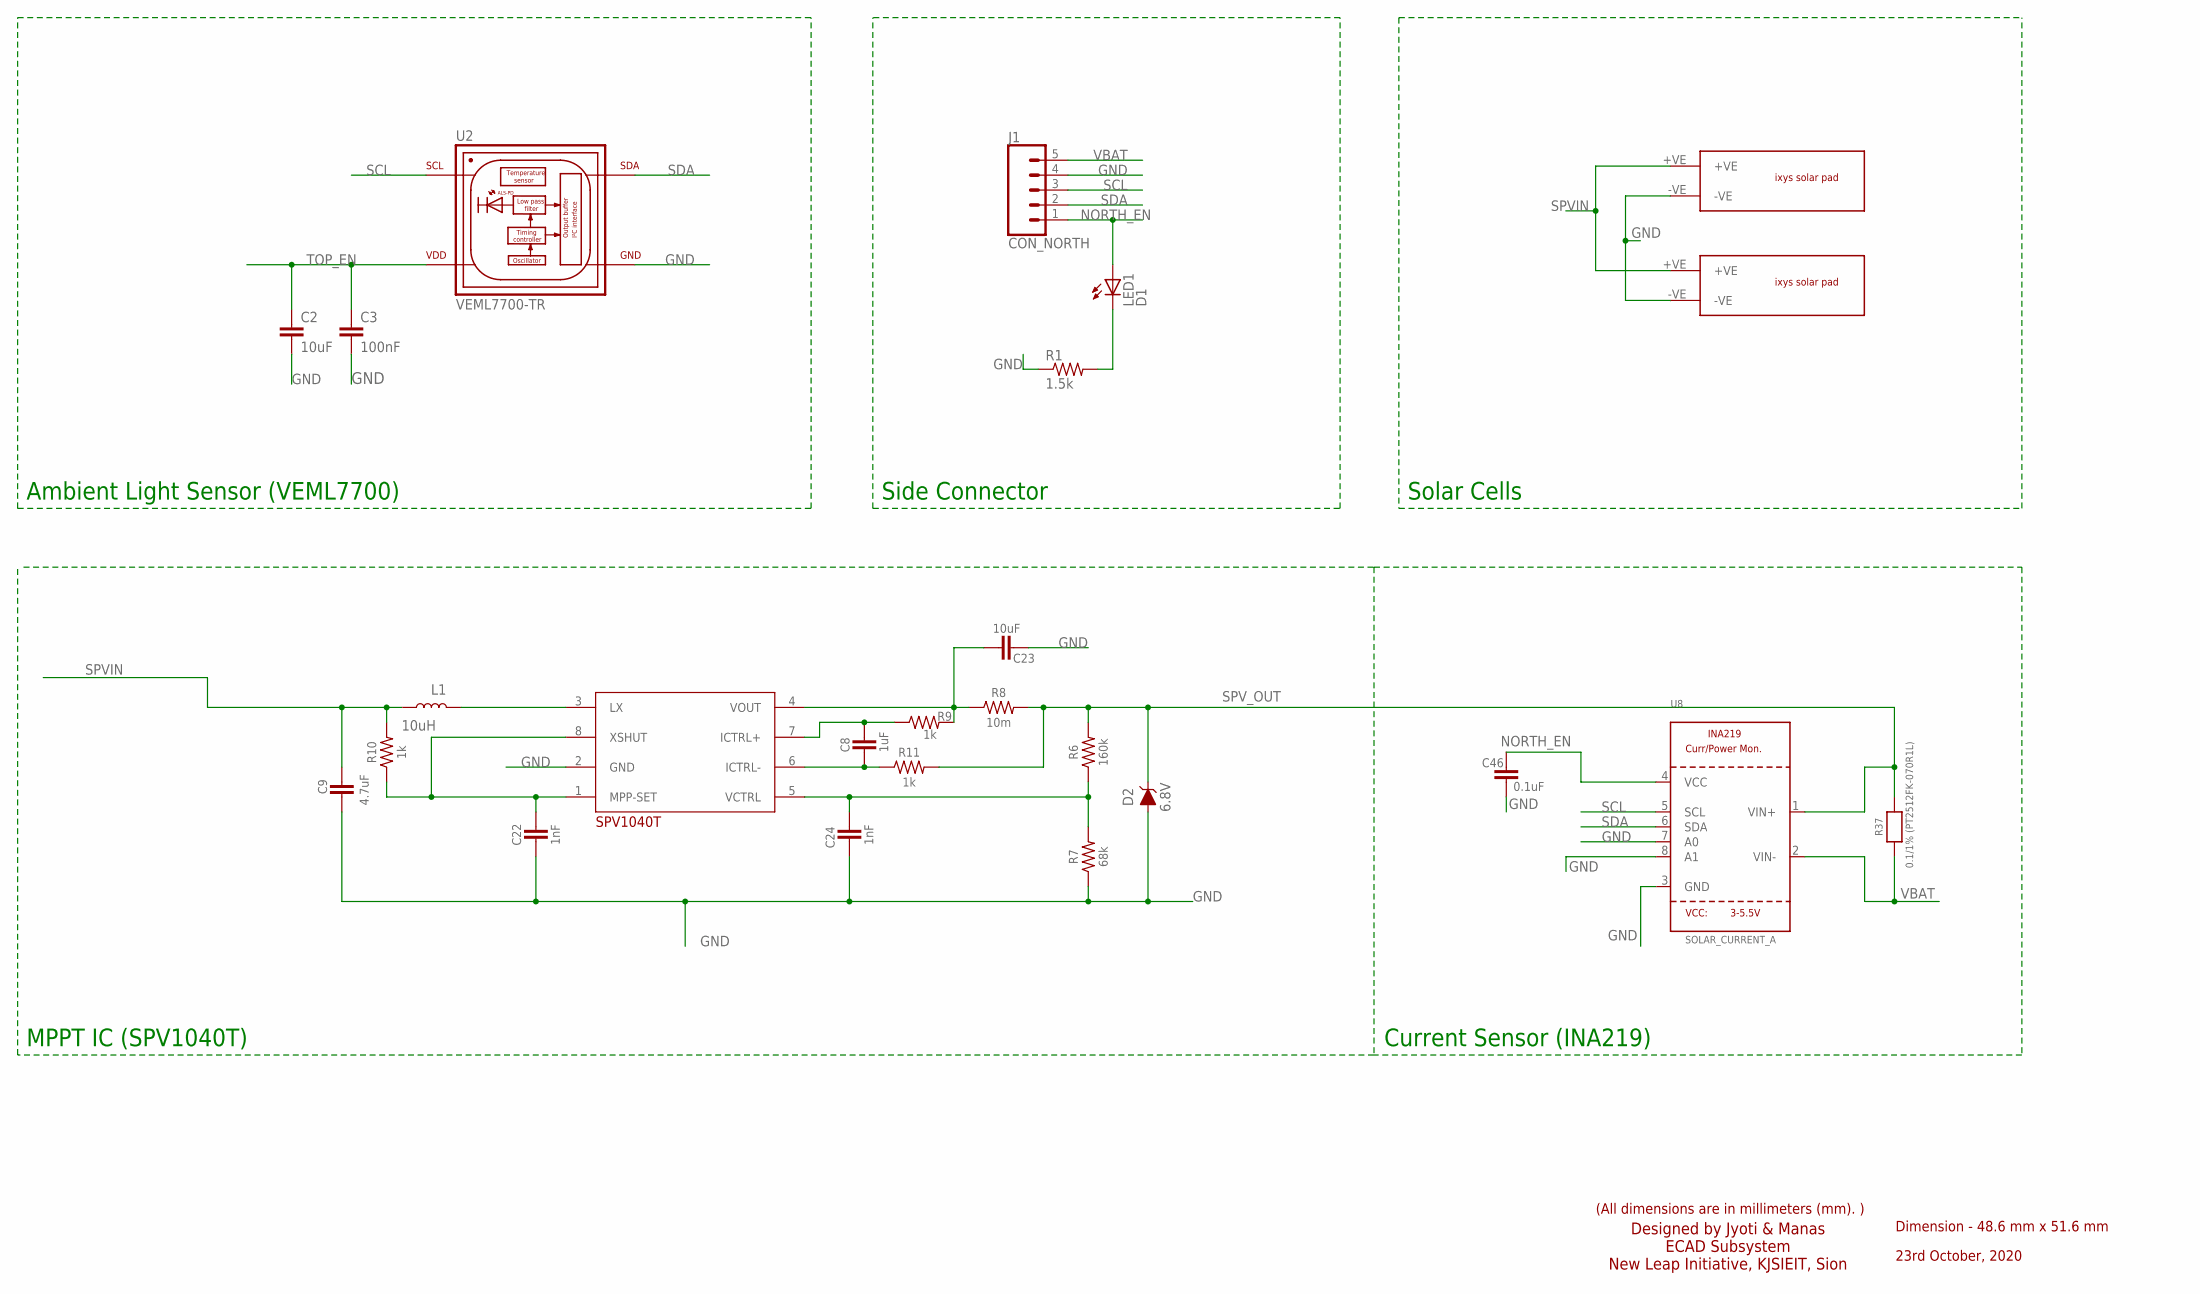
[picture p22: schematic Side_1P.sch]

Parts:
C2, C23: 10uF; 0603
C3: 100nF; 0603
C8: 1uF; 0603
C9: 4.7uF; 0603
C22, C24: 1nF; 0603
C46: 0.1uF; 0603
D2: 6.8V; SOD-323
J1: CON_NORTH; 1X05_1.27MM
L1: 10uH; 0603
LED1: D1; CHIP-LED0603
R1: 1.5k; R0603
R6: 160k; RES_0603
R7: 68k; RES_0603
R8: 10m; RES_0603
R9, R10, R11: 1k; RES_0603
R37: 0.1/1% (PT2512FK-070R1L); 2512
SPV_A: SPV1040T_; SOP65P640X120-8N
U2: VEML7700-TR; XDCR_VEML7700-TR
U8: SOLAR_CURRENT_A; SOT23-8
U$1, U$2: IXYS

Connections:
GND: C2.2, C3.2, C9.2, C22.2, C23.2, C24.2, C46.2, D2.A, J1.4, R1.1, R7.1, SPV_A.2 (GND), U2.3 (GND), U8.3 (GND), U8.7 (A0), U8.8 (A1), U$1.-VE, U$2.-VE
unnamed: LED1.C, R1.2
unnamed: L1.2, SPV_A.3 (LX)
unnamed: C22.1, R10.1, SPV_A.1 (MPP-SET), SPV_A.8 (XSHUT)
unnamed: C24.1, R6.1, R7.2, SPV_A.5 (VCTRL)
unnamed: C8.2, R11.1, SPV_A.6 (ICTRL-)
unnamed: C8.1, R9.1, SPV_A.7 (ICTRL+)
unnamed: C23.1, R8.1, R9.2, SPV_A.4 (VOUT)
NORTH_EN: C46.1, J1.1, LED1.A, U8.4 (VCC)
SCL: J1.3, U2.1 (SCL), U8.5 (SCL)
SDA: J1.2, U2.4 (SDA), U8.6 (SDA)
SPVIN: C9.1, L1.1, R10.2, U$1.+VE, U$2.+VE
SPV_OUT: D2.C, R6.2, R8.2, R11.2, R37.2, U8.1 (VIN+)
TOP_EN: C2.1, C3.1, U2.2 (VDD)
VBAT: J1.5, R37.1, U8.2 (VIN-)

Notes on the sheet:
Ambient Light Sensor (VEML7700)
Side Connector
Solar Cells
MPPT IC (SPV1040T)
Current Sensor (INA219)
Dimension - 48.6 mm x 51.6 mm
23rd October, 2020
(All dimensions are in millimeters (mm). )
Designed by Jyoti & Manas ECAD Subsystem New Leap Initiative, KJSIEIT, Sion

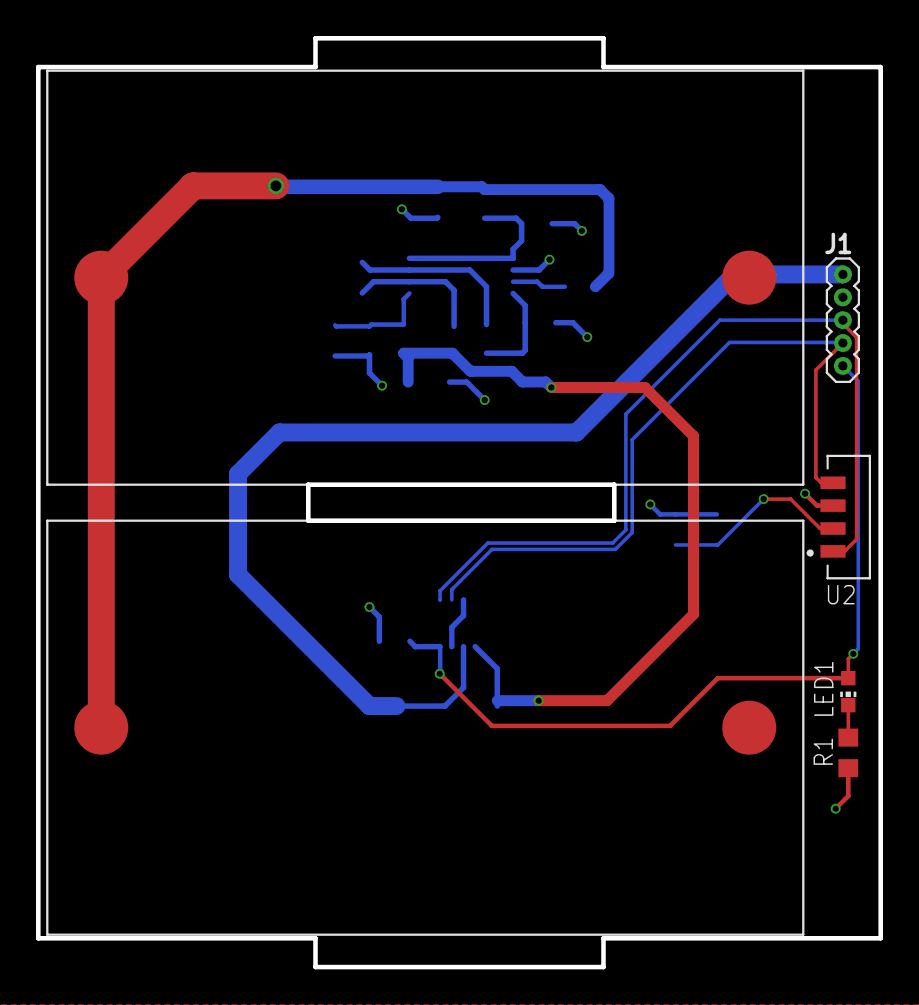
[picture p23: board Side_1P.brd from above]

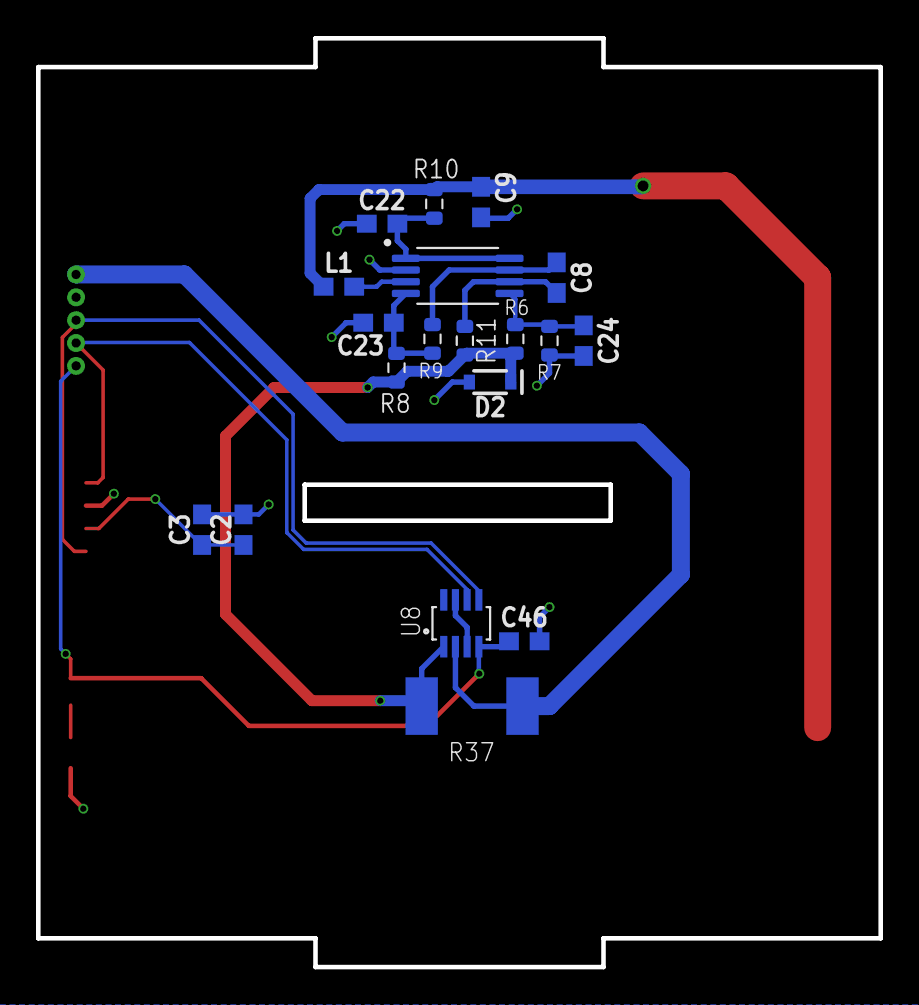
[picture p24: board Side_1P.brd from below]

Board: 2 copper layers, 46.8 x 51.6 mm, 25 parts (19 on the bottom side), 15 nets.

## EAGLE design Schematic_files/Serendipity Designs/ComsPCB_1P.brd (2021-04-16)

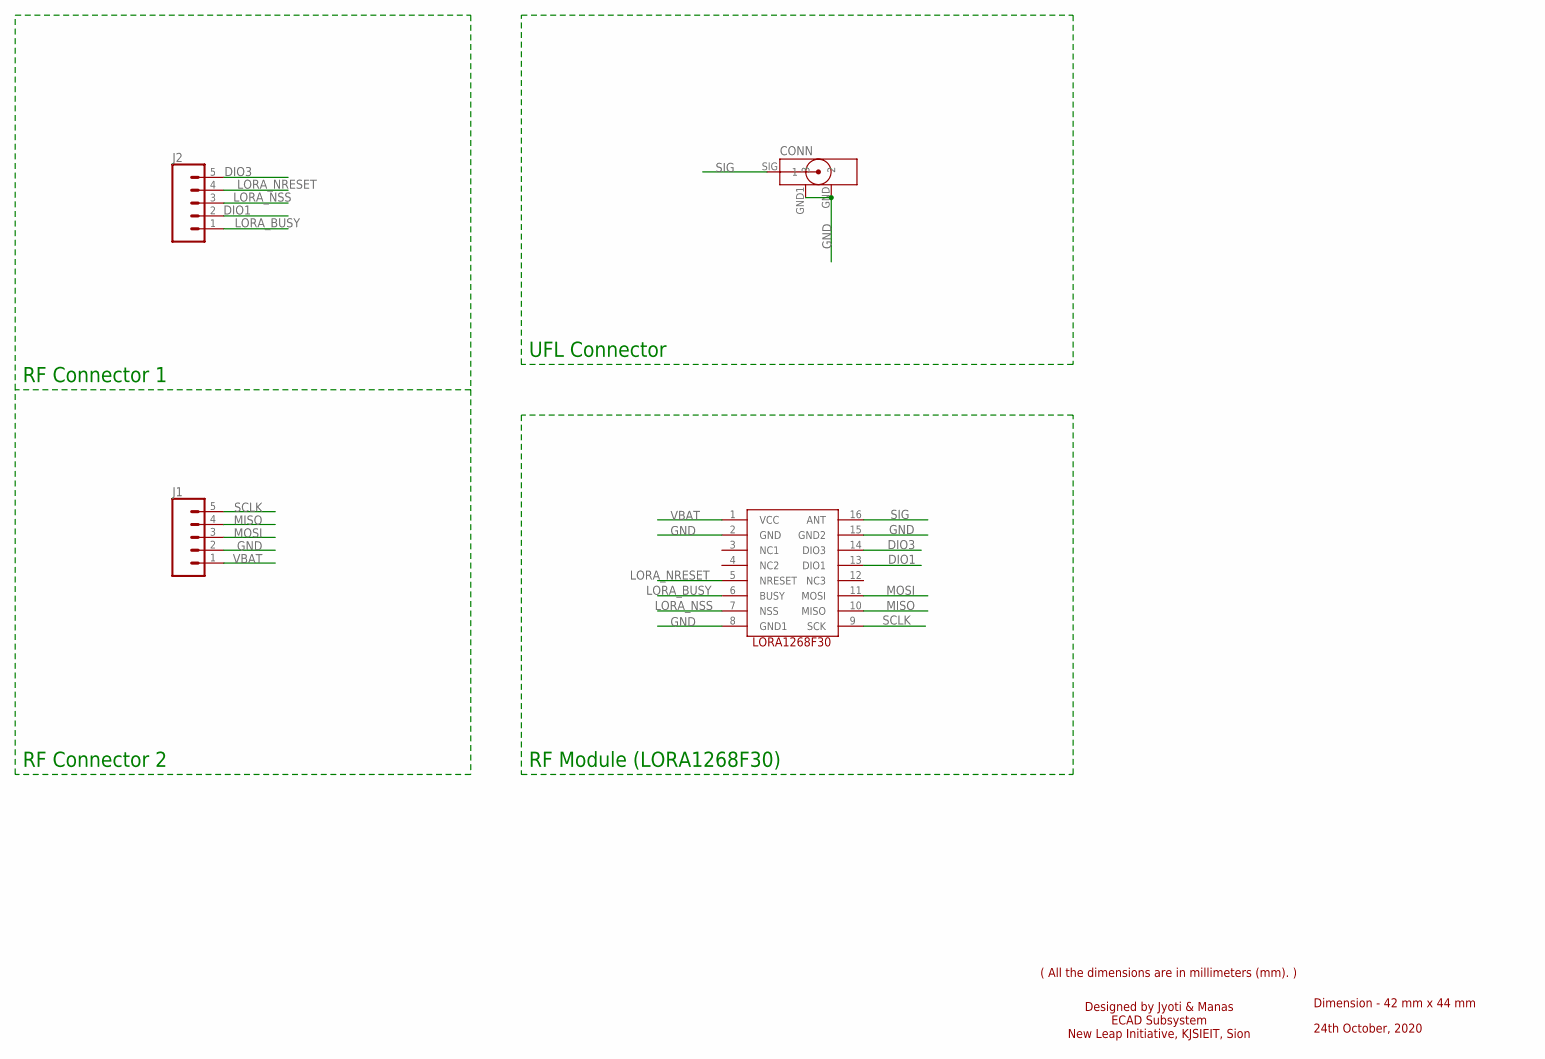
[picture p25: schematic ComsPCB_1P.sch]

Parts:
CONN: U.FL-R-SMT(10)
J1, J2: CONN_051.27MM; 1X05_1.27MM
U$1: U1; LORA1268F30

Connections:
DIO1: J2.2, U$1.13 (DIO1)
DIO3: J2.5, U$1.14 (DIO3)
GND: CONN.GND (2), CONN.GND1 (3), J1.2, U$1.2 (GND), U$1.8 (GND1), U$1.15 (GND2)
LORA_BUSY: J2.1, U$1.6 (BUSY)
LORA_NRESET: J2.4, U$1.5 (NRESET)
LORA_NSS: J2.3, U$1.7 (NSS)
MISO: J1.4, U$1.10 (MISO)
MOSI: J1.3, U$1.11 (MOSI)
SCLK: J1.5, U$1.9 (SCK)
SIG: CONN.SIG (1), U$1.16 (ANT)
VBAT: J1.1, U$1.1 (VCC)

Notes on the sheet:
Dimension - 42 mm x 44 mm
24th October, 2020
( All the dimensions are in millimeters (mm). )
Designed by Jyoti & Manas ECAD Subsystem New Leap Initiative, KJSIEIT, Sion
RF Module (LORA1268F30)
UFL Connector
RF Connector 1
RF Connector 2

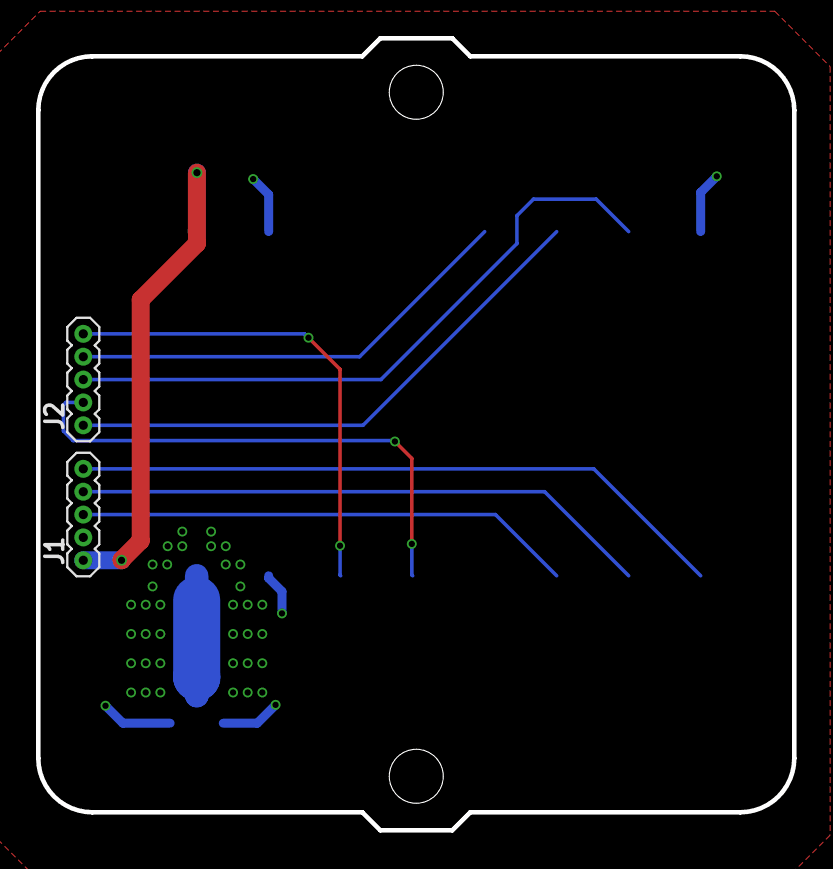
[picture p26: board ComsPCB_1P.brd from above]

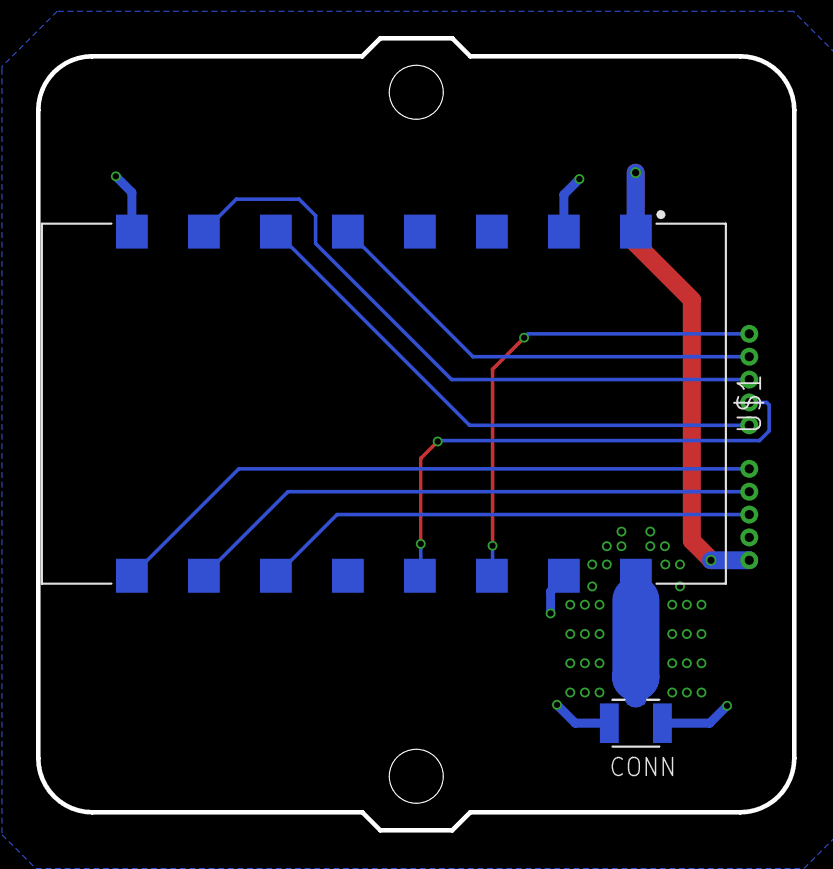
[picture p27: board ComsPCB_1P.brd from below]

Board: 2 copper layers, 42.0 x 44.0 mm, 4 parts (2 on the bottom side), 11 nets.

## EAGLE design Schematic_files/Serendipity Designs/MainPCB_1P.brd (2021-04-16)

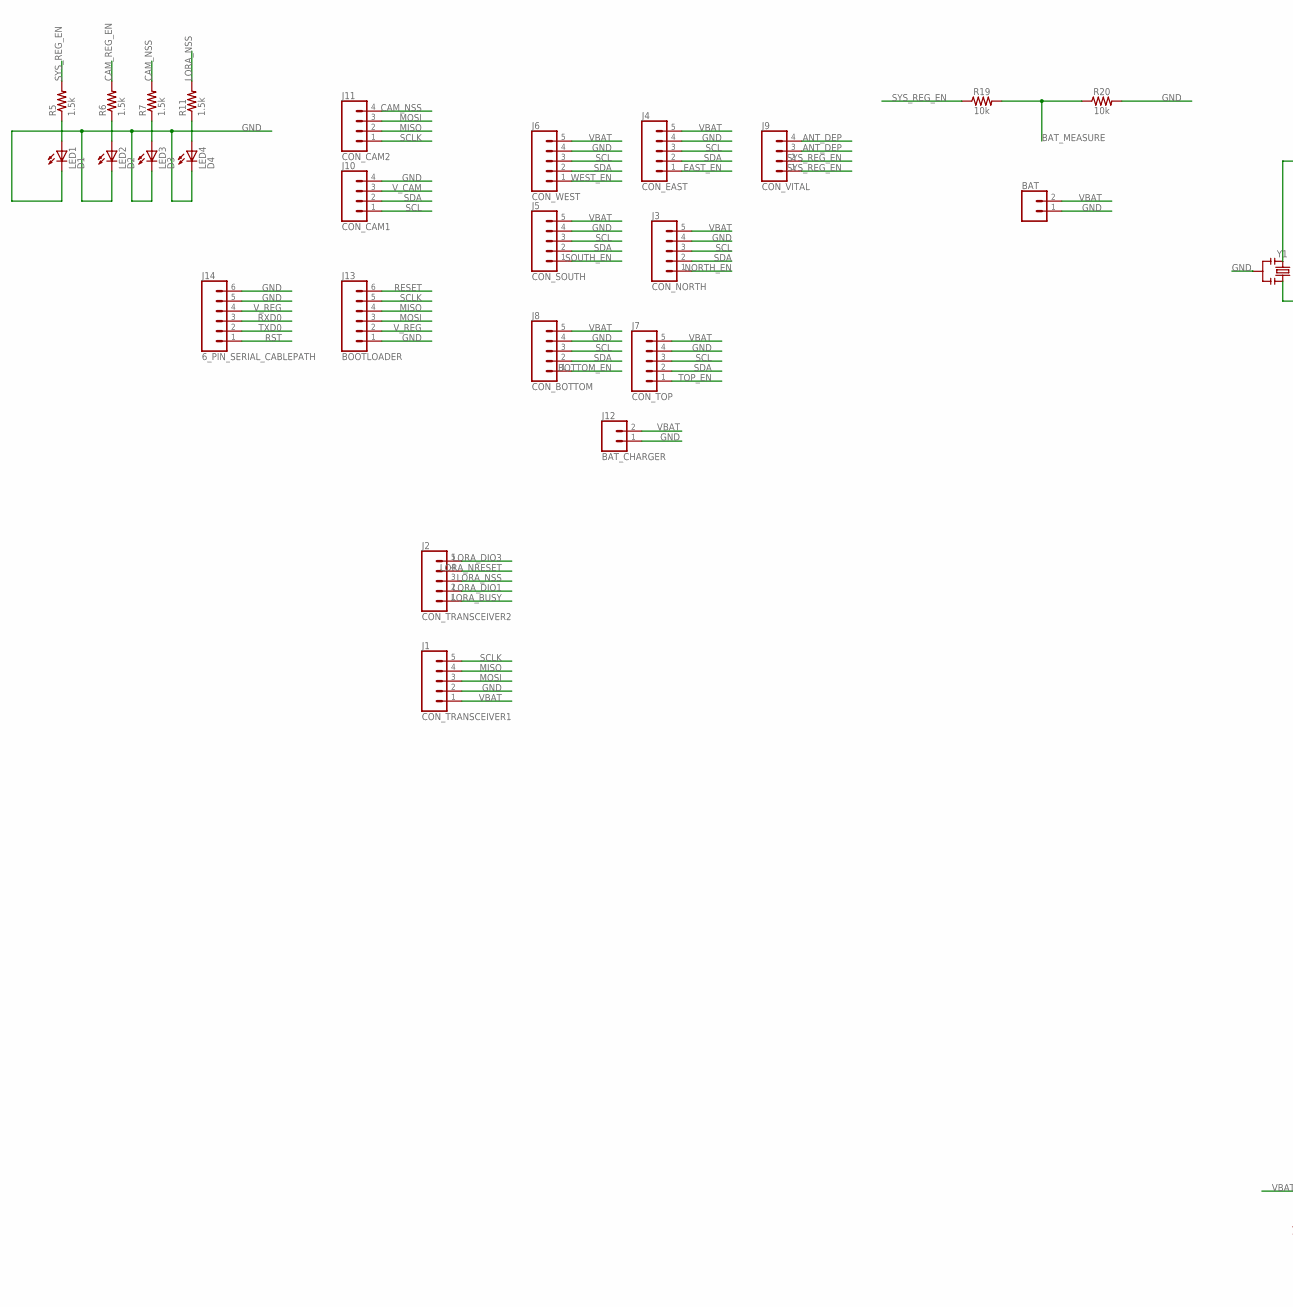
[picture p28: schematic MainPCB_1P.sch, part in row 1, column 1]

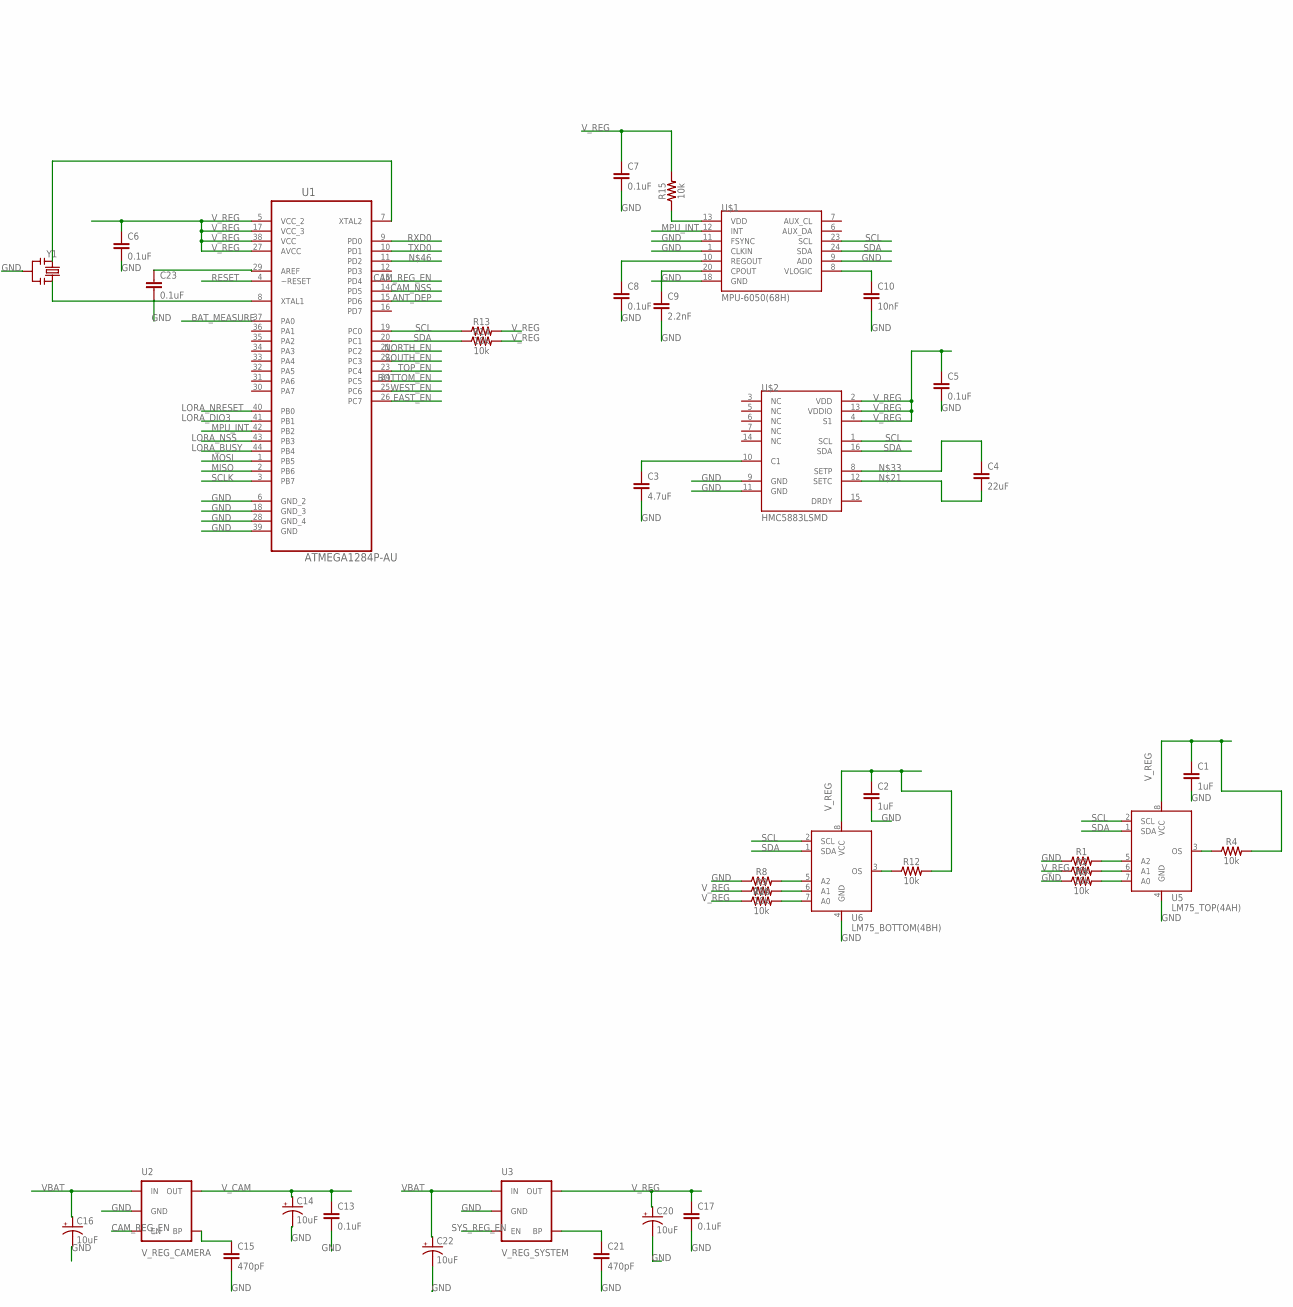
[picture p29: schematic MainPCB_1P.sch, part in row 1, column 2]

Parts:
BAT: CONN_02; 1X02
C1, C2: 1uF; 0603
C3: 4.7uF; 0603
C4: 22uF; 0603
C5, C6, C7, C8, C13, C17: 0.1uF; 0603
C9: 2.2nF; 0603
C10: 10nF; 0603
C14, C16, C20, C22: 10uF; 0603-POLAR
C15, C21: 470pF; 0603
C23: 0.1uF; 0603-CAP
J1: CON_TRANSCEIVER1; 1X05_1.27MM
J2: CON_TRANSCEIVER2; 1X05_1.27MM
J3: CON_NORTH; 1X05_1.27MM
J4: CON_EAST; 1X05_1.27MM
J5: CON_SOUTH; 1X05_1.27MM
J6: CON_WEST; 1X05_1.27MM
J7: CON_TOP; 1X05_1.27MM
J8: CON_BOTTOM; 1X05_1.27MM
J9: CON_VITAL; 1X04_1.27MM
J10: CON_CAM1; 1X04_1.27MM
J11: CON_CAM2; 1X04_1.27MM
J12: BAT_CHARGER; 1X02_NO_SILK
J13: BOOTLOADER; 1X06_1.27MM
J14: 6_PIN_SERIAL_CABLEPATH; 1X06_1.27MM
LED1: D1; CHIP-LED0603
LED2: D2; CHIP-LED0603
LED3: D3; CHIP-LED0603
LED4: D4; CHIP-LED0603
R1, R2, R3, R4, R8, R9, R10, R12, R13, R14, R15, R19, R20: 10k; 0603
R5, R6, R7, R11: 1.5k; R0603
U1: ATMEGA1284P-AU; QFP80P1200X1200X120-44N
U2: V_REG_CAMERA; SOT23-5
U3: V_REG_SYSTEM; SOT23-5
U5: LM75_TOP(4AH); SOT505-1
U6: LM75_BOTTOM(4BH); SOT505-1
U$1: MPU-6050(68H); QFN-24-4MM2
U$2: HMC5883LSMD; 16LPCC
Y1: RESONATORSMD; RESONATOR-SMD

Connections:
ANT_DEP: J9.3, J9.4, U1.15 (PD6)
BAT_MEASURE: R19.2, R20.1, U1.37 (PA0)
BOTTOM_EN: J8.1, U1.24 (PC5)
CAM_NSS: J11.4, R7.2, U1.14 (PD5)
CAM_REG_EN: R6.2, U1.13 (PD4), U2.3 (EN)
EAST_EN: J4.1, U1.26 (PC7)
GND: BAT.1, C1.2, C2.2, C3.2, C5.2, C6.2, C7.2, C8.2, C9.2, C10.2, C13.2, C14.-, C15.2, C16.-, C17.2, C20.-, C21.2, C22.-, C23.2, J1.2, J3.4, J4.4, J5.4, J6.4, J7.4, J8.4, J10.4, J12.1, J13.1, J14.5, J14.6, LED1.C, LED2.C, LED3.C, LED4.C, R1.1, R3.1, R8.1, R20.2, U1.6 (GND_2), U1.18 (GND_3), U1.28 (GND_4), U1.39 (GND), U2.2 (GND), U3.2 (GND), U5.4 (GND), U6.4 (GND), U$1.1 (CLKIN), U$1.9 (AD0), U$1.11 (FSYNC), U$1.18 (GND), U$2.9 (GND), U$2.11 (GND), Y1.2
LORA_BUSY: J2.1, U1.44 (PB4)
LORA_DIO1: J2.2
LORA_DIO3: J2.5, U1.41 (PB1)
LORA_NRESET: J2.4, U1.40 (PB0)
LORA_NSS: J2.3, R11.2, U1.43 (PB3)
MISO: J1.4, J11.2, J13.4, U1.2 (PB6)
MOSI: J1.3, J11.3, J13.3, U1.1 (PB5)
MPU_INT: U1.42 (PB2), U$1.12 (INT)
unnamed: C23.1, U1.29 (AREF)
unnamed: R1.2, U5.5 (A2)
unnamed: U1.7 (XTAL2), Y1.1
unnamed: U1.8 (XTAL1), Y1.3
unnamed: C3.1, U$2.10 (C1)
unnamed: C9.1, U$1.20 (CPOUT)
unnamed: C8.1, U$1.10 (REGOUT)
unnamed: R15.1, U$1.13 (VDD)
unnamed: R2.2, U5.6 (A1)
unnamed: C10.1, U$1.8 (VLOGIC)
unnamed: R8.2, U6.5 (A2)
unnamed: R9.2, U6.6 (A1)
unnamed: R10.2, U6.7 (A0)
unnamed: R3.2, U5.7 (A0)
unnamed: C4.2, U$2.12 (SETC)
unnamed: R4.1, U5.3 (OS)
unnamed: C21.1, U3.4 (BP)
unnamed: LED1.A, R5.1
unnamed: LED2.A, R6.1
unnamed: C15.1, U2.4 (BP)
unnamed: LED3.A, R7.1
unnamed: LED4.A, R11.1
unnamed: C4.1, U$2.8 (SETP)
unnamed: R12.1, U6.3 (OS)
NORTH_EN: J3.1, U1.21 (PC2)
RESET: J13.6, U1.4 (~RESET)
RST: J14.1
RXD0: J14.3, U1.9 (PD0)
SCL: J3.3, J4.3, J5.3, J6.3, J7.3, J8.3, J10.1, R13.1, U1.19 (PC0), U5.2 (SCL), U6.2 (SCL), U$1.23 (SCL), U$2.1 (SCL)
SCLK: J1.5, J11.1, J13.5, U1.3 (PB7)
SDA: J3.2, J4.2, J5.2, J6.2, J7.2, J8.2, J10.2, R14.1, U1.20 (PC1), U5.1 (SDA), U6.1 (SDA), U$1.24 (SDA), U$2.16 (SDA)
SOUTH_EN: J5.1, U1.22 (PC3)
SYS_REG_EN: J9.1, J9.2, R5.2, R19.1, U3.3 (EN)
TOP_EN: J7.1, U1.23 (PC4)
TXD0: J14.2, U1.10 (PD1)
VBAT: BAT.2, C16.+, C22.+, J1.1, J3.5, J4.5, J5.5, J6.5, J7.5, J8.5, J12.2, U2.1 (IN), U3.1 (IN)
V_CAM: C13.1, C14.+, J10.3, U2.5 (OUT)
V_REG: C1.1, C2.1, C5.1, C6.1, C7.1, C17.1, C20.+, J13.2, J14.4, R2.1, R4.2, R9.1, R10.1, R12.2, R13.2, R14.2, R15.2, U1.5 (VCC_2), U1.17 (VCC_3), U1.27 (AVCC), U1.38 (VCC), U3.5 (OUT), U5.8 (VCC), U6.8 (VCC), U$2.2 (VDD), U$2.4 (S1), U$2.13 (VDDIO)
WEST_EN: J6.1, U1.25 (PC6)

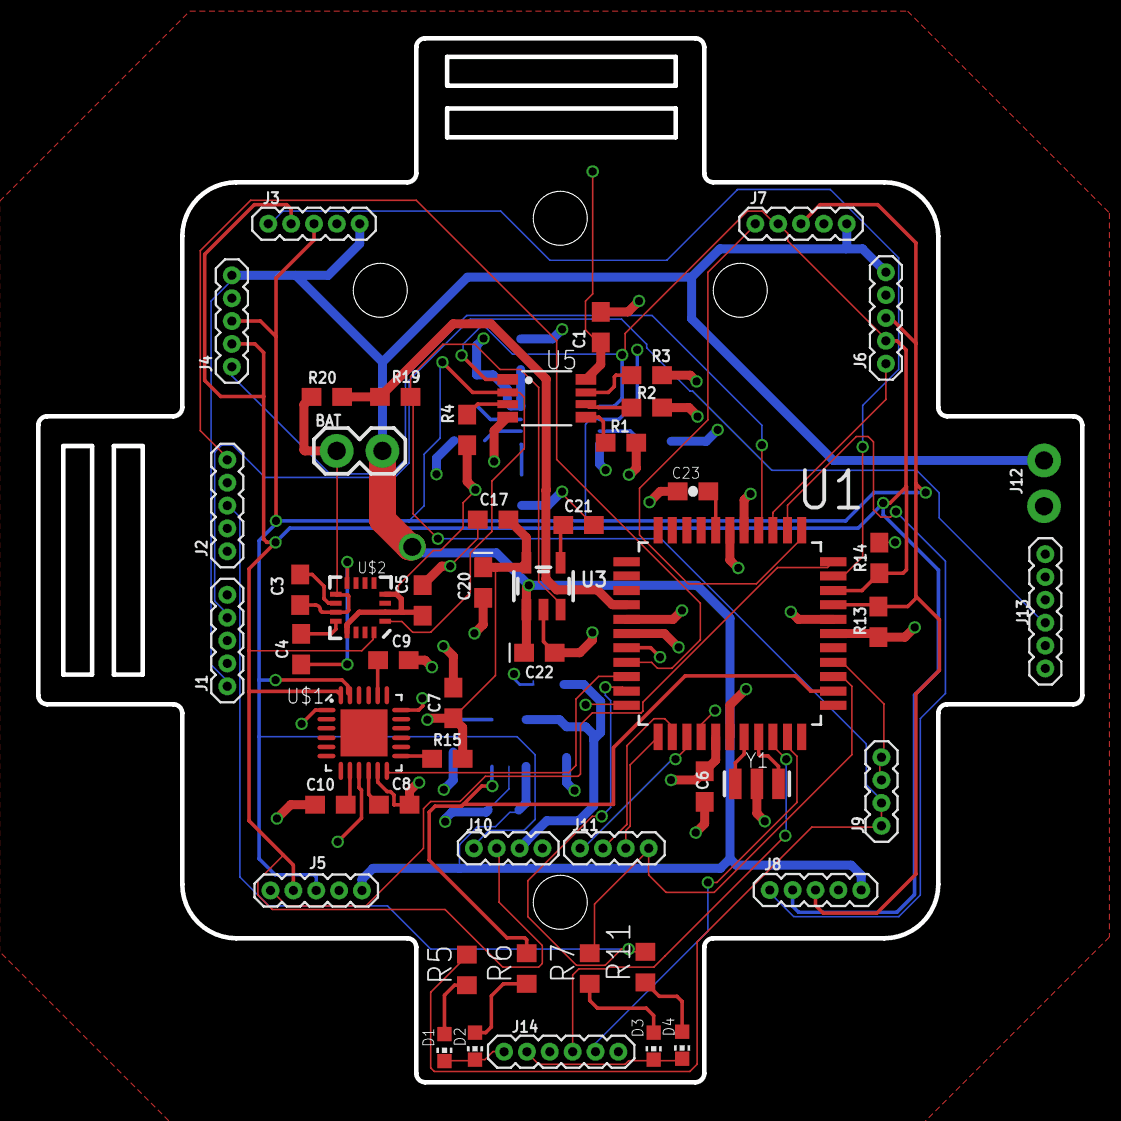
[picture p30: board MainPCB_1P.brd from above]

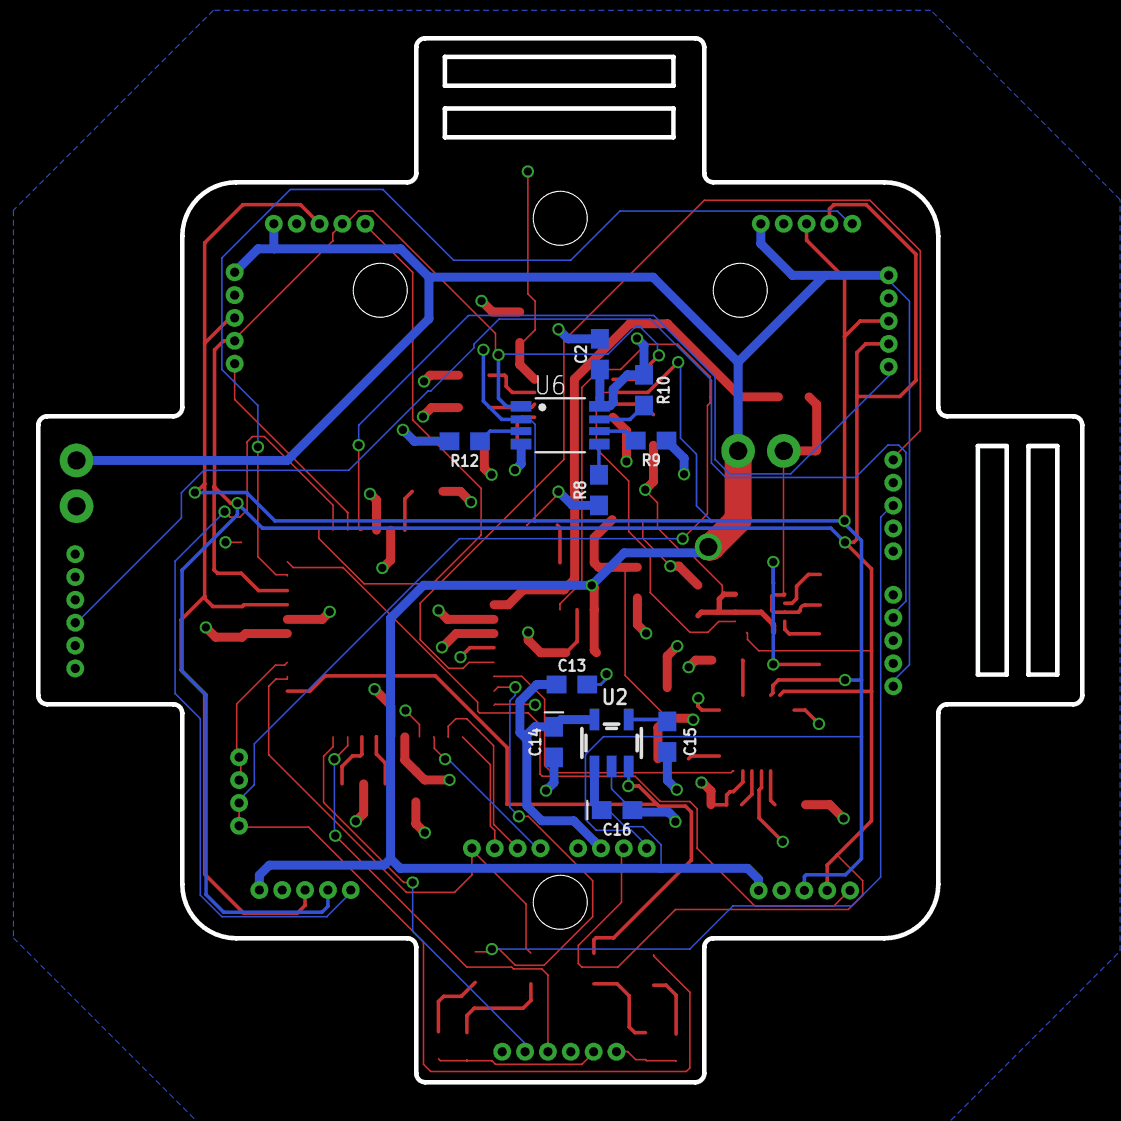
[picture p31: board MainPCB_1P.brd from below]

Board: 4 copper layers, 58.0 x 58.0 mm, 63 parts (11 on the bottom side), 52 nets.

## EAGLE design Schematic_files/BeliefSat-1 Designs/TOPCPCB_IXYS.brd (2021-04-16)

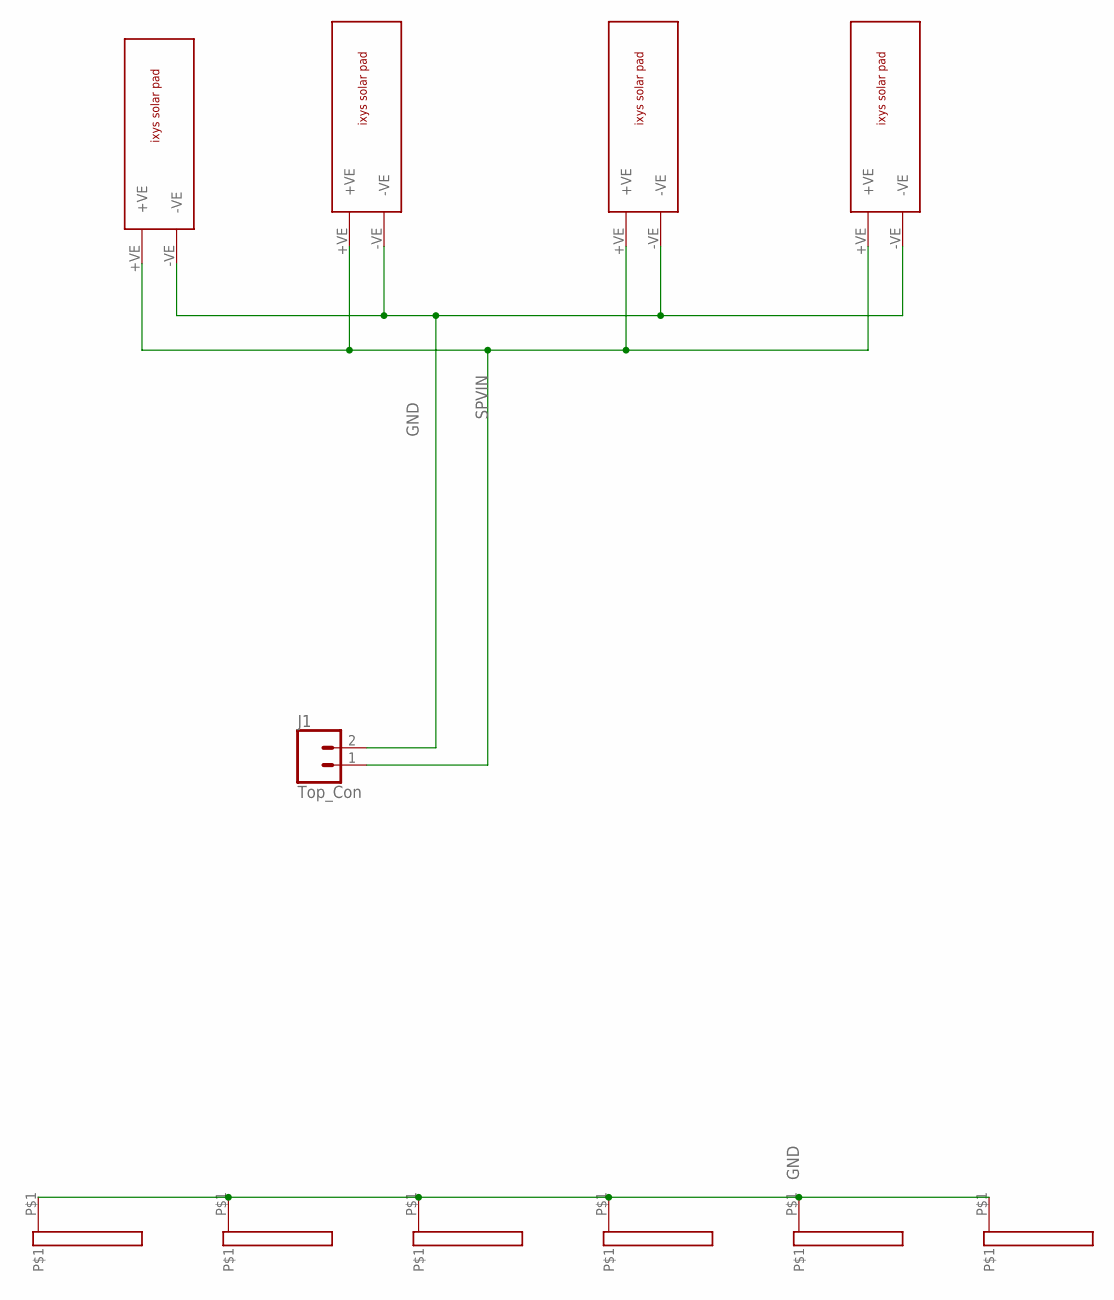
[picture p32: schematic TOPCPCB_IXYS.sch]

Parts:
J1: Top_Con; 1X02
LEFTSOLD: 16X2
U$1, U$4, U$5, U$7, U$9: 16X2
U$2, U$3, U$6, U$8: IXYS

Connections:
GND: J1.2, LEFTSOLD.P$1, U$1.P$1, U$2.-VE, U$3.-VE, U$4.P$1, U$5.P$1, U$6.-VE, U$7.P$1, U$8.-VE, U$9.P$1
SPVIN: J1.1, U$2.+VE, U$3.+VE, U$6.+VE, U$8.+VE

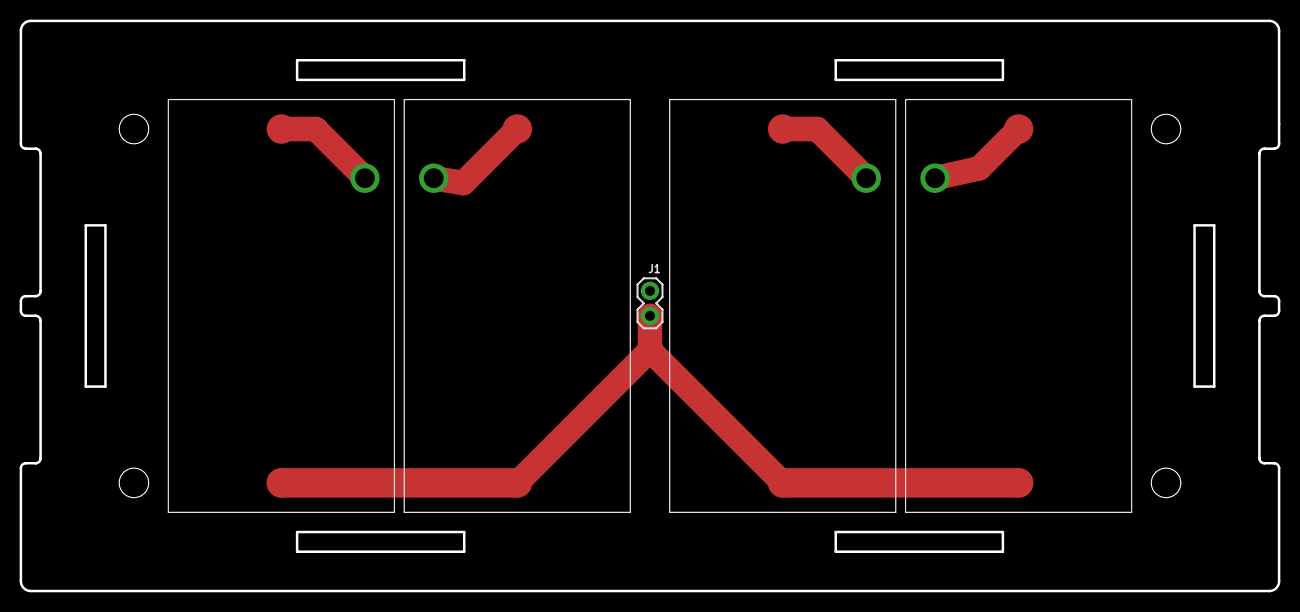
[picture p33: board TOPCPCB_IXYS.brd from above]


Board: 2 copper layers, 128.0 x 58.0 mm, 11 parts (6 on the bottom side), 2 nets.

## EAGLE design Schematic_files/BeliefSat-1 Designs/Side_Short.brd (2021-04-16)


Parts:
J1: CONN_02; 1X02
U$1, U$2: IXYS
U$3, U$4: 16X2

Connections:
GND: J1.2, U$1.-VE, U$2.-VE, U$3.P$1, U$4.P$1
SPVIN: J1.1, U$1.+VE, U$2.+VE


Board: 2 copper layers, 50.0 x 51.6 mm, 5 parts (0 on the bottom side), 2 nets.

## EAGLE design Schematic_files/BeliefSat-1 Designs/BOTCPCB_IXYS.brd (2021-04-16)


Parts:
C1, C2: 100nF; C025-024X044
J1: CONN_05NO_SILK; 1X05_NO_SILK
R2, R4: 10K; 0204/5
R_BURN: 1 Ohm; 0204/5
U$1, U$2, U$4, U$5, U$7, U$8: 16X2
U$3, U$6: OMRON-D2FA; OMRON-D2F-A
U$9, U$11, U$12: IXYS

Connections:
ANT_DRAIN: J1.3, R_BURN.2
GND: C1.2, C2.2, J1.1, U$1.P$1, U$2.P$1, U$3.NO, U$4.P$1, U$5.P$1, U$6.NO, U$7.P$1, U$8.P$1, U$9.-VE, U$11.-VE, U$12.-VE
SPVIN: J1.5, U$9.+VE, U$11.+VE, U$12.+VE
SYS_REG_EN: C1.1, C2.1, J1.4, R2.1, R4.1, U$3.COM, U$6.COM
VOUT: J1.2, R2.2, R4.2, R_BURN.1, U$3.NC, U$6.NC



Board: 2 copper layers, 128.0 x 58.0 mm, 17 parts (5 on the bottom side), 5 nets.

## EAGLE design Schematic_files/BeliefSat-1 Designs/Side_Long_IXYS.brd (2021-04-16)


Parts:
J1: SideLong; 1X02
U$1, U$2, U$3, U$4: 16X2
U$9, U$10, U$11, U$12: IXYS

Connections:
GND: J1.2, U$1.P$1, U$2.P$1, U$3.P$1, U$4.P$1, U$9.-VE, U$10.-VE, U$11.-VE, U$12.-VE
SPVIN: J1.1, U$9.+VE, U$10.+VE, U$11.+VE, U$12.+VE


Board: 2 copper layers, 110.8 x 51.6 mm, 9 parts (0 on the bottom side), 2 nets.

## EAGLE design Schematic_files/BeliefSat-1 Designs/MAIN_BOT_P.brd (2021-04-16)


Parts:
C1, C3: C-EU025-024X044; C025-024X044
C2: CPOL-USE1.8-4; E1,8-4
J3: BAT; 1X02
J4, J5: CONN_01; 1X01
J9: CONN_04PTH; 1X04
Q1, Q2: 2N7000-TO92; TO92
R1: 4.7k; 0204/5
R2, R3, R4, R5, R6, R7, R8, R9, R10, R11: R-US_0204/5; 0204/5
R13: 10k; 0204/5
U1: DRA818U_NEW; DORJI_DRA818U_NEW
U2: DRA818V_NEW; DORJI_DRA818V_NEW
U3: DS18B20; TO-92-AMMO
U$1: ARDUNIO_PRO_MINI; ARDUINOPROMINI
X1, X2: BU-SMA-V

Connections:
A0: C3.2, R9.1, R10.2, U$1.A0
A2: U$1.A2
AF_OUT_VHF: C3.1, U2.3 (AF_OUT)
ANT_DEP: J4.1, U$1.8
ANT_U: U1.12 (ANT), X1.1
ANT_V: U2.12 (ANT), X2.1
D2: R1.1, U3.2 (DQ), U$1.2
D3: Q1.2 (G), R11.2, U$1.3
D4: R5.1, U$1.4
D5: R4.1, U$1.5
D6: R3.1, U$1.6
D7: R2.1, U$1.7
GND: C1.2, J3.2, J9.2, Q1.3 (S), Q2.3 (S), R6.1, R8.1, R10.1, R11.1, R13.1, U1.7 (H/L), U1.9 (GND), U1.10 (GND), U2.9 (GND), U2.10 (GND), U3.1 (GND), X1.2, X1.3 (2), X1.4 (2), X1.5 (2), X2.2, X2.3 (2), X2.4 (2), X2.5 (2)
MICIN_VHF: R7.2, R8.2, U1.3 (AF_OUT), U2.18 (MIC_IN)
unnamed: C2.+, R7.1
unnamed: C1.1, C2.-, R2.2, R3.2, R4.2, R5.2, R6.2
unnamed: Q2.1 (D), U$1.GND, U$1.GND2 (GND), U$1.GND3 (GND), U$1.GND4 (GND), U$1.GND5 (GND)
PTT_VHF: Q1.1 (D), U1.1 (SQ), U2.5 (PTT)
SCL: J9.4, U$1.A5
SDA: J9.3, U$1.A4
SYS_EN: J5.1, Q2.2 (G)
UHF_PD: R13.2, U1.6 (PD), U$1.9
UHF_RX: U1.17 (TXD), U$1.12
UHF_TX: U1.16 (RXD), U$1.13
VBAT: J3.1, U1.8 (VBAT), U2.8 (VBAT), U$1.RAW
VCC: J9.1, R1.2, R9.2, U2.6 (PD), U3.3 (VDD), U$1.VCC, U$1.VCC1 (VCC)
VHF_RX: U2.17 (TXD), U$1.10
VHF_TX: U2.16 (RXD), U$1.11


Board: 2 copper layers, 110.0 x 42.0 mm, 27 parts (0 on the bottom side), 27 nets.

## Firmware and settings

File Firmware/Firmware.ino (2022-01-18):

// ANCHOR MACROS

// ANCHOR Sensor Init
#define i2c_addr_top_temp 0x4A
#define i2c_addr_bot_temp 0x4B
#define i2c_addr_ambient_light 0x44
#define i2c_addr_magnetometer 0x1E
#define i2c_addr_gyro 0x68 // NOTE Address of MPU6050 is 0x68;
#define i2c_addr_power 0x40
#define i2c_addr_fuel_guage 0x36
#define north_enable_pin 18

// ANCHOR LORA
#define LORA_BUSY 4
#define LORA_DIO1 10
#define LORA_NRST 0
#define LORA_NSS 3
#define LORA_DIO3 1

// ANCHOR Camera Macros
#define Camera_enable_pin 12
#define camera_cs_pin 13

// ANCHOR Operating Modes
#define normal_mode 0x11
#define safe_mode 0x05
#define auto_ssdv_mode 0xAA
#define Silent_mode 0XFF

// ANCHOR Telemetry
#define image_quality 5 // NOTE try changing this from 0-7 and see which quality suits the speed;
#define packet_type_telem_pos 0
#define callsign_telem_pos 1
#define resets_telem_pos 7
#define packets_telem_pos 9
#define mode_telem_pos 13
#define temp1_telem_pos 14
#define temp2_telem_pos 16
#define magnetometer_telem_pos 18
#define gyro_telem_pos 24
#define ambient_light_telem_pos 30
#define power_telem_pos 42
#define bat_volt_telem_pos 52
#define soc_telem_pos 54
#define crc_telem_pos 56
#define rs_telem_pos 58
#define radioFreq 435.4
#define telemetry_packet_indicator 0xAB

// ANCHOR Persistent SRAM Macros
#define EEPROM_DATA_ADDR 0x00
#define FIRST_START_DELAY 100 // NOTE In milliseconds
#define PERSISTANCE_CHECKER_VALUE 0xAF

// ANCHOR IMPORTS
#include <Wire.h>
#include <avr/wdt.h> // NOTE Issue in wdt.h file.
#include <util/crc16.h>
#include <Adafruit_INA219.h> // NOTE Added Adafruit_INA219 library
#include <EEPROM.h>
#include <RadioLib.h>
#include <ArduCAM.h>
#include "ssdv.h"
#include "rs8.h"
#include "key.h"

// ANCHOR VARIABLES
uint32_t soft_reset_cnt __attribute__((section(".noinit")));
uint8_t sram_persistance_checker_variable __attribute__((section(".noinit")));
/////////////////////
uint8_t telem_cmd_packet[90], currentmode = safe_mode; //start with safe modes
char callsign_bytes[6] = {'V', 'U', '3', 'O', 'I', 'R'};
uint8_t ccsds_sync_word[4] = {0x1A, 0xCF, 0xFC, 0x1D}, hi_chars[3] = {'H', 'i', '!'}, image_id = 0;
uint32_t no_of_packets = 0;
float battery_soc;
bool received_flag = 0;
uint32_t last_telemetry, last_ssdv;
SX1268 radio = new Module((uint8_t)LORA_NSS, (uint8_t)LORA_DIO1, (uint8_t)LORA_NRST, (uint8_t)LORA_BUSY);
ArduCAM Camera(OV2640, camera_cs_pin);

// ANCHOR STRUCTURES
struct EEprom
{
    bool deployed;
    uint16_t resets;
    uint32_t hard_resets;
    bool silent_mode;
} flag;

// ANCHOR FUNCTIONS;
//this may need changes


// ANCHOR get_temperature();
void get_temperature()
{
    Wire.beginTransmission(i2c_addr_top_temp);
    Wire.write(0x00); //temperature register
    Wire.endTransmission();
    delay(100);
    Wire.requestFrom(i2c_addr_top_temp, 2);
    telem_cmd_packet[temp1_telem_pos] = Wire.read();     //msb of temp
    telem_cmd_packet[temp1_telem_pos + 1] = Wire.read(); //lsb of temp
    wdt_reset();
    delay(100);
    //temp2
    Wire.beginTransmission(i2c_addr_bot_temp);
    Wire.write(0x00); //temperature register
    Wire.endTransmission();
    delay(100);
    Wire.requestFrom(i2c_addr_bot_temp, 2);
    telem_cmd_packet[temp2_telem_pos] = Wire.read();     //msb of temp
    telem_cmd_packet[temp2_telem_pos + 1] = Wire.read(); //lsb of temp
    wdt_reset();
}

// ANCHOR get_ambient_light();
void get_ambient_light()
{
    for (int i = 0; i < 6; i++) //toggles through all the sensors
    {
        digitalWrite(north_enable_pin + i, HIGH); //enables the sensor
        delay(100);                               //wait for the sensor to settle down before reading
        Wire.beginTransmission(i2c_addr_ambient_light);
        Wire.write(0x00); //result register
        Wire.endTransmission();
        delay(100);
        Wire.requestFrom(i2c_addr_ambient_light, 2);
        telem_cmd_packet[ambient_light_telem_pos + (2 * i)] = Wire.read();     //MSB of get_ambient_light
        telem_cmd_packet[ambient_light_telem_pos + (2 * i) + 1] = Wire.read(); //LSB of get_ambient_light
        wdt_reset();
        digitalWrite(north_enable_pin + i, LOW); //disables sensor
    }
}

// ANCHOR get_magnetometer();
void get_magnetometer()
{
    Wire.beginTransmission(i2c_addr_magnetometer);
    Wire.write(0x03); //starting address
    Wire.endTransmission();
    delay(100);
    Wire.requestFrom(i2c_addr_magnetometer, 6);
    for (int i = 0; i < 3; i++)
    {
        telem_cmd_packet[magnetometer_telem_pos + (2 * i)] = Wire.read();     //mag MSB
        telem_cmd_packet[magnetometer_telem_pos + (2 * i) + 1] = Wire.read(); //mag LSB
        wdt_reset();
    }
}

// ANCHOR get_gyro();
void get_gyro()
{
    Wire.beginTransmission(i2c_addr_gyro);
    Wire.write(0x43);
    Wire.endTransmission();
    delay(100);
    Wire.requestFrom(i2c_addr_gyro, 6);
    for (int i = 0; i < 3; i++)
    {
        telem_cmd_packet[gyro_telem_pos + (2 * i)] = Wire.read();     //gyro MSB
        telem_cmd_packet[gyro_telem_pos + (2 * i) + 1] = Wire.read(); //gyro LSB
        wdt_reset();
    }
}

// ANCHOR get_solar_power();
void get_solar_power()
{
    for (int i = 0; i < 5; i++)
    {
        digitalWrite(north_enable_pin + i, HIGH);
        delay(100);

        Adafruit_INA219 ina219;
        ina219.begin();
        ina219.setCalibration_16V_400mA();

        //configure
        Wire.beginTransmission(i2c_addr_power);
        Wire.write(0x00); //config register
        Wire.write(0x01);
        Wire.write(0x9F); //configuration calculated as (019F)H for 16V400ma range
        Wire.endTransmission();
        delay(100); //let the setting sink in
        Wire.beginTransmission(i2c_addr_power);
        Wire.write(0x03); //power register
        Wire.endTransmission();
        delay(100);
        Wire.requestFrom(i2c_addr_power, 2);
        telem_cmd_packet[power_telem_pos + (2 * i)] = Wire.read();     //MSB POWER
        telem_cmd_packet[power_telem_pos + (2 * i) + 1] = Wire.read(); //LSB POWER
        wdt_reset();
        digitalWrite(north_enable_pin + i, LOW); //disable the panel
    }
}

// ANCHOR get_battery_soc();
void get_battery_soc()
{
    Wire.beginTransmission(i2c_addr_fuel_guage);
    Wire.write(0x04); //soc register
    Wire.endTransmission();
    delay(100);
    Wire.requestFrom(i2c_addr_fuel_guage, 2);
    telem_cmd_packet[soc_telem_pos] = Wire.read();
    telem_cmd_packet[soc_telem_pos + 1] = Wire.read();
    wdt_reset();
    battery_soc = telem_cmd_packet[soc_telem_pos] + (float)(telem_cmd_packet[soc_telem_pos + 1] / 256.0);
    if (battery_soc <= 50.0 && (currentmode != safe_mode || currentmode != Silent_mode))
    {
        currentmode = safe_mode; // auto switch to safe mode when battery goes less than 50%
    }
    if (currentmode == safe_mode && battery_soc >= 85.0 && currentmode != Silent_mode)
    {
        currentmode = normal_mode; //auto switch to normal mode when battery goes more than 70%
    }
    wdt_reset();
}

// ANCHOR get_battery_volt();
void get_battery_volt()
{
    Wire.beginTransmission(i2c_addr_fuel_guage);
    Wire.write(0x02);
    Wire.endTransmission();
    delay(100);
    telem_cmd_packet[bat_volt_telem_pos] = Wire.read();
    telem_cmd_packet[bat_volt_telem_pos + 1] = Wire.read();
}

// ANCHOR get_sensor_values();
void get_sensor_values()
{
    get_temperature();
    get_ambient_light();
    get_magnetometer();
    get_gyro();
    get_solar_power();
    get_battery_soc();
    get_battery_volt();
    memcpy(&telem_cmd_packet[packets_telem_pos], &no_of_packets, 4);
    telem_cmd_packet[mode_telem_pos] = currentmode;
    memcpy(&telem_cmd_packet[resets_telem_pos], &flag.resets, 2);
    memcpy(&telem_cmd_packet[callsign_telem_pos], &callsign_bytes, 6);
}

// ANCHOR telemetry();
void telemetry()
{
    telem_cmd_packet[packet_type_telem_pos] = telemetry_packet_indicator; //indicates telemetry packet
    get_sensor_values();
    uint16_t crc = 0xffff;
    for (int i = 0; i < crc_telem_pos; i++)
    {
        crc = _crc_ccitt_update(crc, telem_cmd_packet[i]);
    }
    memcpy(&telem_cmd_packet[crc_telem_pos], &crc, 2);
    encode_rs_8(&telem_cmd_packet[0], &telem_cmd_packet[rs_telem_pos], (223 - 58));
    int output_power;
    currentmode == safe_mode ? output_power = 13 : output_power = 16;
    radio.beginFSK(radioFreq, 1.2, 0.3, 14.6, output_power, 140, 64, 0.5, 0); // FIXME The unexpected 140.
    radio.transmit(telem_cmd_packet, 90);
    delay(100);
    radio.startReceive();
}

// ANCHOR receive_interrupt();
void receive_interrupt()
{
    if (received_flag)
    {
        return;
    }
    received_flag = true;
}

// ANCHOR transmit_ssdv();
void transmit_ssdv()
{
    //Start camera and capture pic
    digitalWrite(Camera_enable_pin, HIGH);
    delay(1000); //let camera turn on properly
    //reset cpld of camera
    Camera.write_reg(0x07, 0x08);
    delay(100);
    Camera.write_reg(0x07, 0x00);
    delay(100);
    Camera.set_format(JPEG);
    Camera.InitCAM();
    Camera.clear_fifo_flag();
    Camera.OV2640_set_JPEG_size(OV2640_1600x1200);
    Camera.start_capture();
    //get sensors during camera capture proceeds and transmit
    telem_cmd_packet[packet_type_telem_pos] = 0xCD; //to indicate camera orientation frame
    get_sensor_values();
    uint16_t crc = 0xffff;
    for (int i = 0; i < crc_telem_pos; i++)
    {
        crc = _crc_ccitt_update(crc, telem_cmd_packet[i]);
    }
    encode_rs_8(&telem_cmd_packet[0], &telem_cmd_packet[rs_telem_pos], (223 - 58));
    radio.beginFSK(radioFreq, 1.2, 0.3, 14.6, 16, 140, 64, 0.5, 0);
    radio.transmit(telem_cmd_packet, 90);
    delay(2000);
    while (!(Camera.get_bit(ARDUCHIP_TRIG, CAP_DONE_MASK)))
    {
    }
    //read fifo and convert to ssdv and send
    radio.beginFSK(radioFreq, 9.6, 2.4, 25, 16, 140, 64, 0.5, 0); //set to 9600 gmsk
    radio.fixedPacketLengthMode(255);                             //increases the packet size for ssdv transmissions
    uint8_t ssdv_packet[256], image_buffer[64];
    bool done = false;
    static ssdv_t ssdv;
    int r;
    uint8_t temp = 0, temp_last = 0;
    ssdv_enc_init(&ssdv, SSDV_TYPE_NORMAL, callsign_bytes, image_id++, image_quality);
    ssdv_enc_set_buffer(&ssdv, &ssdv_packet[0]);
    while (!done)
    {
        while ((r = ssdv_enc_get_packet(&ssdv)) == SSDV_FEED_ME)
        {
            Camera.CS_LOW();
            Camera.set_fifo_burst();
            int i = 0;
            while (i < 64) //take image 64 byte
            {
                temp_last = temp;
                temp = SPI.transfer(0x00);
                if ((temp == 0xD9) && (temp_last == 0xFF)) //check if it is end of the image
                {
                    image_buffer[i] = temp;
                    done = true;
                    digitalWrite(camera_cs_pin, HIGH);
                    digitalWrite(Camera_enable_pin, LOW); //shut the camera down after image is complete
                    break;
                }
                else
                {
                    image_buffer[i] = temp;
                }
                i++;
                wdt_reset();
            }
            ssdv_enc_feed(&ssdv, image_buffer, (i + 1));
            wdt_reset();
            radio.transmit(&ssdv_packet[1], 255); //we don't wont to send [0] as it is sync byte
            wdt_reset();
        }
        wdt_reset();
    }
    radio.fixedPacketLengthMode(90);
    radio.beginFSK(radioFreq, 1.2, 0.3, 14.6, 16, 140, 64, 0.5, 0);
    wdt_reset();
    radio.startReceive();
    wdt_reset();
}

// ANCHOR process_cmd();
void process_cmd()
{
    uint8_t major_part[48];
    memcpy(major_part, telem_cmd_packet, 48);
    int j = decode_rs_8(major_part, 0, 0, 223 - 16);
    if (j < 0)
    {
        return;
    } //discard uplink if the correction fails
    int n = memcmp(&major_part[7], callsign_bytes, 6);
    if (n != 0)
    {
        return;
    }                      //check if the uplink is for the same satellite if not then discard
    switch (major_part[0]) //switch as per the packet packet_type
    {
    case 0xF5: //in case it is digipeater uplink
    {
        if (currentmode != safe_mode)
        {
            //construct digipeater downlink packet
            telem_cmd_packet[packet_type_telem_pos] = 0xFF;                 //digipeater downlink packet indicator
            memcpy(&telem_cmd_packet[1], callsign_bytes, 6);                //put satellite callsign
            memcpy(&telem_cmd_packet[7], &major_part[1], 6);                //put sender callsign
            memcpy(&telem_cmd_packet[13], hi_chars, 3);                     //say hi before the message
            memcpy(&telem_cmd_packet[16], &telem_cmd_packet[48], 42);       //copy the message in place
            encode_rs_8(telem_cmd_packet, &telem_cmd_packet[58], 223 - 58); //get rs parity
            wdt_reset();
            radio.transmit(telem_cmd_packet, 90); //transmit the digipeater downlink
            delay(50);
            radio.startReceive(); //put the transceiver in reception mode again
            delay(50);
            wdt_reset();
        }
        return;
    }
    case 0xEF: //if it is internal command
    {
        //decrypting the command
        major_part[15] ^= private_key;
        major_part[14] ^= major_part[15];
        major_part[13] ^= major_part[14];
        wdt_reset();
        if (major_part[13] == 0x15 && major_part[14] == 0x12) //command to reset satellite
        {
            while (1)
            {
            } //make an infinite loop so that watchdog resets the MCU
        }
        if (major_part[13] == 0xAA && major_part[14] == 0xBD) // command for transmitting ssdv once
        {

            transmit_ssdv();
            wdt_reset();
            return;
        }
        if (major_part[13] == 0xCD && major_part[14] == 0x99) //command to shift to automatic ssdv mode
        {
            if (currentmode == safe_mode)
            {
                return;
            }
            currentmode = auto_ssdv_mode; //shift to automatic ssdv mode
            wdt_reset();
            return;
        }
        if (major_part[13] == 0xAB && major_part[14] == 0xCD) //command to shift to normal mode
        {
            currentmode = normal_mode; //shift to normal mode
            wdt_reset();
            return;
        }
        if (major_part[13] == 0xDE && major_part[14] == 0x55) //command to shift to safe mode
        {
            currentmode = safe_mode; //shift to safe mode
            wdt_reset();
            return;
        }
        if (major_part[13] == 0x55 && major_part[14] == 0xAA) //shift to silent mode
        {
            currentmode = Silent_mode;
            wdt_reset();
            flag.silent_mode = true;
            EEPROM.put(0x00, flag);
            return;
        }
        if (major_part[13] == 0xAA && major_part[14] == 0x55) //turn on transmitter
        {
            currentmode = normal_mode;
            wdt_reset();
            return;
        }
    }
    default:
        return;
    }
}

// ANCHOR VOID SETUP();
void setup()
{
    // EEPROM.get(flag, 0x00);

    SPI.begin();

    //Set EEPROM Flags
    EEPROM.get(0x00, flag);
    if (flag.resets == 0x00)
    {
        delay(FIRST_START_DELAY);
    }
    flag.resets++;
    if (sram_persistance_checker_variable != PERSISTANCE_CHECKER_VALUE) // NOTE Check if there was a hard reset.
    {
        flag.hard_resets++;
        sram_persistance_checker_variable = PERSISTANCE_CHECKER_VALUE;
        soft_reset_cnt = 0;
    }
    else
    {
        soft_reset_cnt++;
    }
    EEPROM.put(0x00, flag);
    Wire.begin();

    //initialize the magnetometer in continuous mode
    
    Wire.beginTransmission(i2c_addr_magnetometer);
    Wire.write(0x02); //the mode register
    Wire.write(0x00); //continuous mode
    Wire.endTransmission();
    delay(100);

    //Wake up MPU6050 gyro
    Wire.beginTransmission(i2c_addr_gyro);
    Wire.write(0x6B); //power management register
    Wire.write(0x00); //wakes up
    Wire.endTransmission();
    delay(100);

    wdt_enable(WDTO_8S); // NOTE Fixed unresolved import in wdt library;

    radio.setCRC(0);
    radio.setSyncWord(ccsds_sync_word, 4);
    radio.fixedPacketLengthMode(90);
    radio.setDio1Action(receive_interrupt); // NOTE Fixed function call
    if (flag.silent_mode)
    {
        currentmode = Silent_mode;
    }
}

// ANCHOR VOID LOOP();
void loop()
{
    if (received_flag)
    {
        radio.readData(telem_cmd_packet, 90);
        wdt_reset();
        process_cmd();
        wdt_reset();
        received_flag = false;
    }
    switch (currentmode)
    {
    case normal_mode:
    {
        if (abs(last_telemetry - millis()) >= 30000)
        {
            wdt_reset();
            telemetry();
            wdt_reset();
            last_telemetry = millis();
            break;
        }
    }
    case safe_mode:
    {
        if (abs(last_telemetry - millis()) >= 55000)
        {
            wdt_reset();
            telemetry();
            wdt_reset();
            last_telemetry = millis();
            break;
        }
    }
    case auto_ssdv_mode:
    {
        if (abs(last_telemetry - millis()) >= 30000)
        {
            wdt_reset();
            telemetry();
            wdt_reset();
            last_telemetry = millis();
        }
        if (abs(last_ssdv - millis()) >= 600000)
        {
            wdt_reset();
            transmit_ssdv();
            wdt_reset();
            last_ssdv = millis();
            break;
        }
    }
    }
}

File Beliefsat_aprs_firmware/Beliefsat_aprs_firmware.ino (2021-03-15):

#include <Adafruit_INA219.h>
#include <Adafruit_MPU6050.h>
#include <DallasTemperature.h>
#include <EEPROM.h>
#include <LibAPRS.h>
#include <OneWire.h>
#include <SoftwareSerial.h>
#include <Wire.h>
#include <avr/wdt.h>

#define ADC_REFERENCE REF_3V3
#define OPEN_SQUELCH true
#define debug

#define SATCALL_SIGN "VU2CWN"
#define GSCALL_SIGN "VU3OIR"
#define SATTELEM_SSID 11
#define SATDIGI_SSID 6
#define GS_SSID 1
#define FIRST_BOOT_DELAY 1800     // seconds
#define RESISTOR_BURN_DELAY 10000 // milliseconds
#define TELEMETRY_INTERVAL 60000  // milliseconds
#define APRS_TOCALL "CQ"

#define ANTENNA_DEPLOYMENT_PIN (8)
#define UHF_POWER_DOWN_PIN (9)
#define UHF_RX (12)
#define UHF_TX (13)
#define VHF_RX (10)
#define VHF_TX (11)
#define TEMPERATURE_SENSOR_PIN 2

String temp_sensor_1 = "";
String temp_sensor_2 = "";
String gyro_sensor_1 = "";
String gyro_sensor_2 = "";
String gyro_sensor_3 = "";
String current = "";
String battery_voltage = "";

#define VHF_SETUP_STRING "AT+DMOSETGROUP=0,145.8250,145.8250,0000,0,0000\r\n"
#define UHF_SETUP_STRING "AT+DMOSETGROUP=0,435.6000,435.6000,0000,1,0001\r\n"
#define TURN_OFF_VOICE_REPEATER_INPUT digitalWrite(UHF_POWER_DOWN_PIN, LOW)
#define TURN_ON_VOICE_REPEATER_INPUT                                           \
  do {                                                                         \
    digitalWrite(UHF_POWER_DOWN_PIN, HIGH);                                    \
    uhf_port.write(F(UHF_SETUP_STRING));                                       \
  } while (0)

#define TOTAL_RESETS_EEPROM_ADDR 0x00
#define WD_INDUCED_RESETS_EEPROM_ADDR 0x02
#define TX_STATUS 0x04

#define COMMAND_INDICATOR '!'

OneWire oneWire(TEMPERATURE_SENSOR_PIN);
DallasTemperature sensors(&oneWire);
SoftwareSerial vhf_port(VHF_RX, VHF_TX);
SoftwareSerial uhf_port(UHF_RX, UHF_TX);

boolean gotPacket = false;
AX25Msg incomingPacket;
uint8_t *packetData;
boolean digipeater_is_on = false;
boolean voice_repeater_is_on = false;
boolean transmission_is_on;
uint16_t total_resets;
uint16_t wd_induced_resets;
long last_telemetry_time;

// initialize sensor objects
Adafruit_MPU6050 mpu;
Adafruit_INA219 ina219;

String num_to_string(uint8_t X)
{
  String str = "";
  if(X < 10)
    {
      String str = "00" + String(X, DEC);
    }
    if(X < 100 && X > 9)
    {
      String str = "0" + String(X, DEC);
    }
    if(X >= 100)
    {
      String str = String(X, DEC);
    }
   return str;
}

String float_to_string(float value){
    long X,temp = 0;
    X = (long)(value * 100);
    temp = X % 100;
    X = X - temp;
    String str = num_to_string(X);
    return str;
}

void aprs_msg_callback(struct AX25Msg *msg) {
  if (!gotPacket) {
    gotPacket = true;
    memcpy(&incomingPacket, msg, sizeof(AX25Msg));
    if (freeMemory() > msg->len) {
      packetData = (uint8_t *)malloc(msg->len);
      memcpy(packetData, msg->info, msg->len);
      incomingPacket.info = packetData;
    } else {
      gotPacket = false;
    }
  }
}

ISR(WDT_vect) {
  wd_induced_resets++;
  EEPROM.write(WD_INDUCED_RESETS_EEPROM_ADDR, wd_induced_resets);
}

void setup() {
#ifdef debug
  Serial.begin(9600);
#endif
  watchdogSetup();
  EEPROM.get(TOTAL_RESETS_EEPROM_ADDR, total_resets);

  if (total_resets < 1) {
#ifdef debug
    Serial.println(F("First_boot_delay started"));
#endif
    for (int i = 0; i < FIRST_BOOT_DELAY; i++) {
      delay(1000);
      wdt_reset();
    }
    pinMode(ANTENNA_DEPLOYMENT_PIN, OUTPUT);
    digitalWrite(ANTENNA_DEPLOYMENT_PIN, HIGH);
    delay(RESISTOR_BURN_DELAY / 2);
    wdt_reset();
    delay(RESISTOR_BURN_DELAY / 2);
    digitalWrite(ANTENNA_DEPLOYMENT_PIN, LOW);
  }

  total_resets++;
  EEPROM.put(TOTAL_RESETS_EEPROM_ADDR, total_resets);
  EEPROM.get(WD_INDUCED_RESETS_EEPROM_ADDR, wd_induced_resets);
  EEPROM.get(TX_STATUS, transmission_is_on);

  pinMode(UHF_POWER_DOWN_PIN, OUTPUT);

  vhf_port.begin(9600);
  uhf_port.begin(9600);

  vhf_port.write(F(VHF_SETUP_STRING));
  wdt_reset();
  APRS_init(ADC_REFERENCE, OPEN_SQUELCH);
  APRS_setCallsign(SATCALL_SIGN, SATTELEM_SSID);
  APRS_setDestination(APRS_TOCALL, 0);

#ifdef debug
  APRS_printSettings();
  Serial.print(F("Free RAM:     "));
  Serial.println(freeMemory());
#endif
  Wire.begin();
  ////////////////////////////////////
  // Sensor initializations
  wdt_reset();

  //MPU6050
  mpu.begin();
  mpu.setAccelerometerRange(MPU6050_RANGE_8_G);
  mpu.setGyroRange(MPU6050_RANGE_500_DEG);
  mpu.setFilterBandwidth(MPU6050_BAND_21_HZ);

  //INA219
  ina219.begin();

  //Dallas temperature sensor
  
  ////////////////////////////////////
  last_telemetry_time = millis();
}

void processPacket() {
  if (gotPacket) {
    gotPacket = false;
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

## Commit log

2020-05-11 Update test-compile.yml
    Added Arduino:avr to the build step to that avr g++ file exists
2020-05-29 Schematic files for the design created for proposal for PS4 Orbital Platform
    [MainCPCB003.brd, MainCPCB003.csv, MainCPCB003.sch]
2020-05-29 SIde plates, top and bottom plates for the design
    [BOTCPCB.brd, BOTCPCB.sch, Side_Long.brd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]
2020-07-24 Update README.md
    Changed the sensor data format in the light of additional solar cells
2020-12-01 Adding Light sensor code with header file
2020-12-01 Create gyrosensor.ino
    Code for gyrosensor MPU6050
2021-01-24 Fixed errors in imports and function call.
    Updated the annoying code indentation.
    [Firmware.ino]
2021-01-31 Fixed a few errors in Firmware.ino
    [Firmware.ino]
2021-02-10 Fixed issue with macros
    [Firmware.ino]
2021-02-22 Reset counts in persistent SRAM
    [BuildOpt.h, Firmware.ino, Lightsensor.ino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]

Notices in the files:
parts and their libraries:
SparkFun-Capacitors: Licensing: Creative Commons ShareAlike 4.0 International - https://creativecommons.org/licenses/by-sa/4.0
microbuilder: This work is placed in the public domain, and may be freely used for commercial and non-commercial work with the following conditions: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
